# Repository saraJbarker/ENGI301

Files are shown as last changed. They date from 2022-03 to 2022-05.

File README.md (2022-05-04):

<h1>ENGI301</h1>
Repository for ENGI301 course work
<h3>Project 1</h3>
The project_1 folder contains the code for the PocketBeagle Medication Dispenser, found on my Hackster: https://www.hackster.io/sarajbarker/pocketbeagle-medication-dispenser-ca1f8f </br> </br>
All of the hardware can be found on the Hackster page. For the code, the only file needed is <a href=https://github.com/saraJbarker/ENGI301/blob/main/project_1/main_code3.py"">main_code3.py</a>. 
To set up and run this code: </br>
<ol>
  <li> Wire everything up according to the directions on Hackster (also see <a href="https://github.com/saraJbarker/ENGI301/blob/main/project_1/sketch_bb.png"> sketch_bb.png</a> for a Fritzing diagram) </li>
  <li> Connect the PocketBeagle to the internet </li>
  <li> Set up the PocketBeagle to run Python: 
    <ul>
      <li><code>sudo apt-get update </code></li>
      <li><code>sudo apt-get install build-essential python-dev python-setuptools python-smbus -y </code></li>
      <li><code>sudo apt-get install python-pip python3-pip -y</code></li>
    </ul>
  <li>Install Adafruit BBIO:
    <ul><code>sudo pip3 install --upgrade Adafruit_BBIO</code></ul>
    </li>
  <li>Drag and drop <a href=https://github.com/saraJbarker/ENGI301/blob/main/project_1/main_code3.py>main_code3.py</a> into your PocketBeagle directory.</li>
  <li>Press "Run".</li>
  </ol>
  </br>
  Included in the Project 1 folder are the STL and Solidworks files for the pillbox - the STL can go into a 3D printing software like 3DprinterOS, or you can modify the Solidworks file and make a new STL file. <a href="https://github.com/saraJbarker/ENGI301/blob/main/project_1/boxv3all.ai">boxv3all.ai</a> is the Illustrator file for the sides of the wooden box. This can be used with a laser cutter to cut the wood out. <a href="https://github.com/saraJbarker/ENGI301/blob/main/project_1/sketch_bb.png">sketch_bb.png</a> is a picture of the Fritzing file. <code>code_skeleton</code>, <code>main_code.py</code>, and <code>main_code2.py</code> are just in progress versions of the currently updated code, <code>main_code3.py</code> - there isn't a need to download these.
  <h3>Project 2</h3>
  The project_2 folder contains files for a PCB that would control the medication dispenser described in Project 1. The library, schematic, and board files in EAGLE are included in the EAGLE subfolder, and the Gerber files are in the MFG subfolder. If you would like to make this PCB, you will need to send the Gerber files to a manufacturer. There is also a PDF version of the schematic and a Bill of Materials inside the project_2 folder. </br>
  <i>Note:</i> the PCB has not been physically made, so there may be errors in the provided files.

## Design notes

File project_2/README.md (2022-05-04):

The EAGLE folder contains the EAGLE files - library, schematic, and board - to create a PCB that can control the medication dispenser in project_01. The MFG folder contains the Gerber files for the PCB. A bill of materials (Barker_project_02_BOM) and a PDF version of the schematic (Barker_project_02.pdf) is also included.

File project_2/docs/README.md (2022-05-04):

This is the folder that contains pictures of the top and bottom layer as seen in gerbv, a Gerber file viewer.

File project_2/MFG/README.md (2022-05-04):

This is the folder for manufacturing files, including Gerber files and pictures of the top and bottom layers (found in the docs folder).

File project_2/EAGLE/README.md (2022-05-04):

This is the folder for all EAGLE files for the PCB.

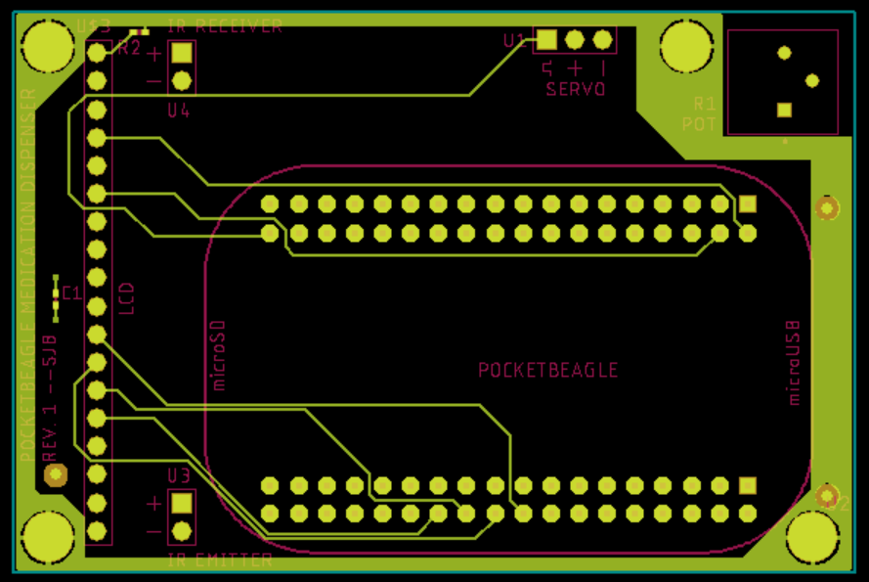
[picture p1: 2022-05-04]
project_2/docs/gerber_file_top.png

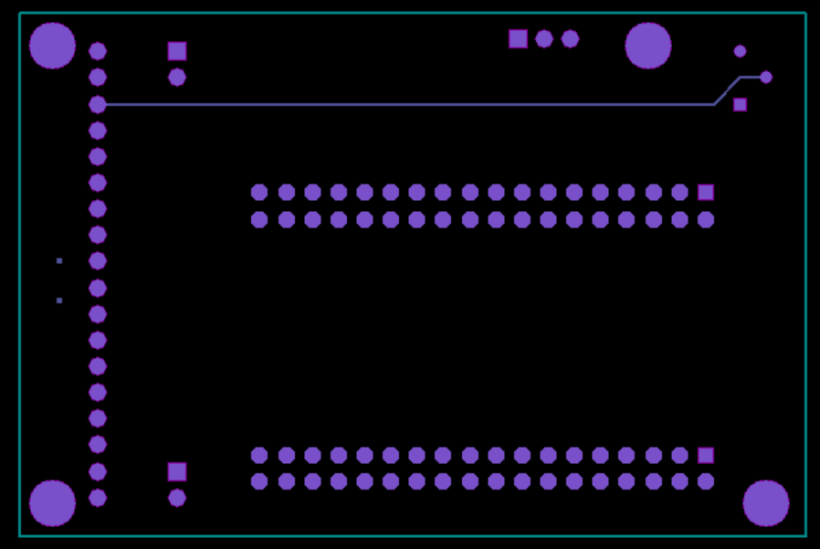
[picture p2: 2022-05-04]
project_2/docs/gerber_file_bottom.png

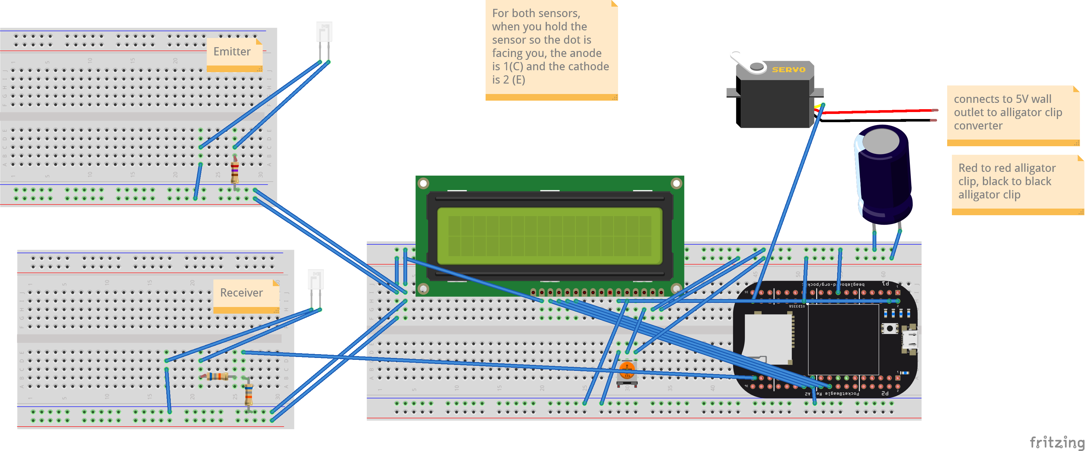
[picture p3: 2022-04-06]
project_1/sketch_bb.png

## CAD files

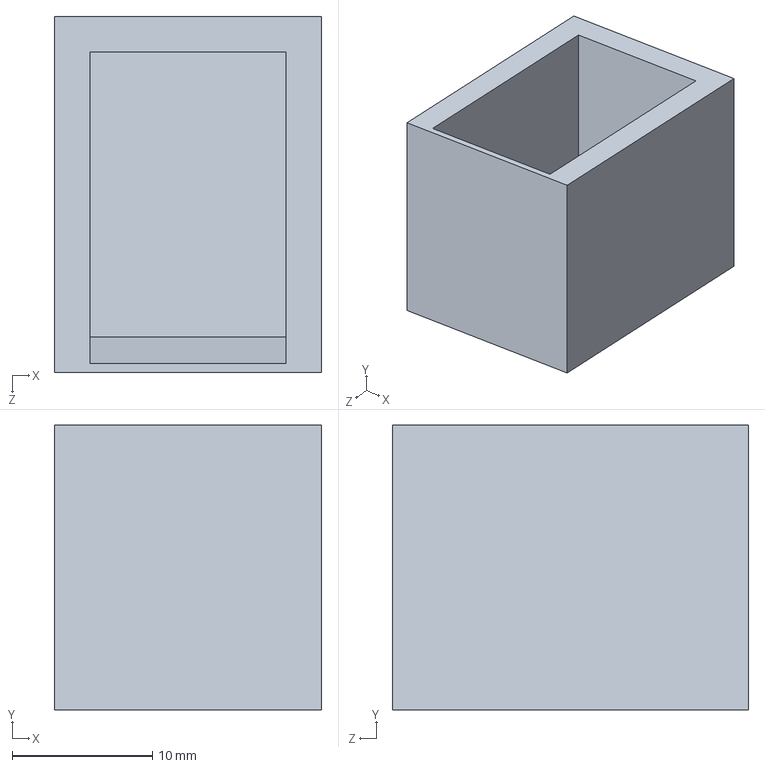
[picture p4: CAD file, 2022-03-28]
project_1/box.SLDPRT
19.1 x 20.3 x 25.4 mm

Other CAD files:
project_1/box.STL

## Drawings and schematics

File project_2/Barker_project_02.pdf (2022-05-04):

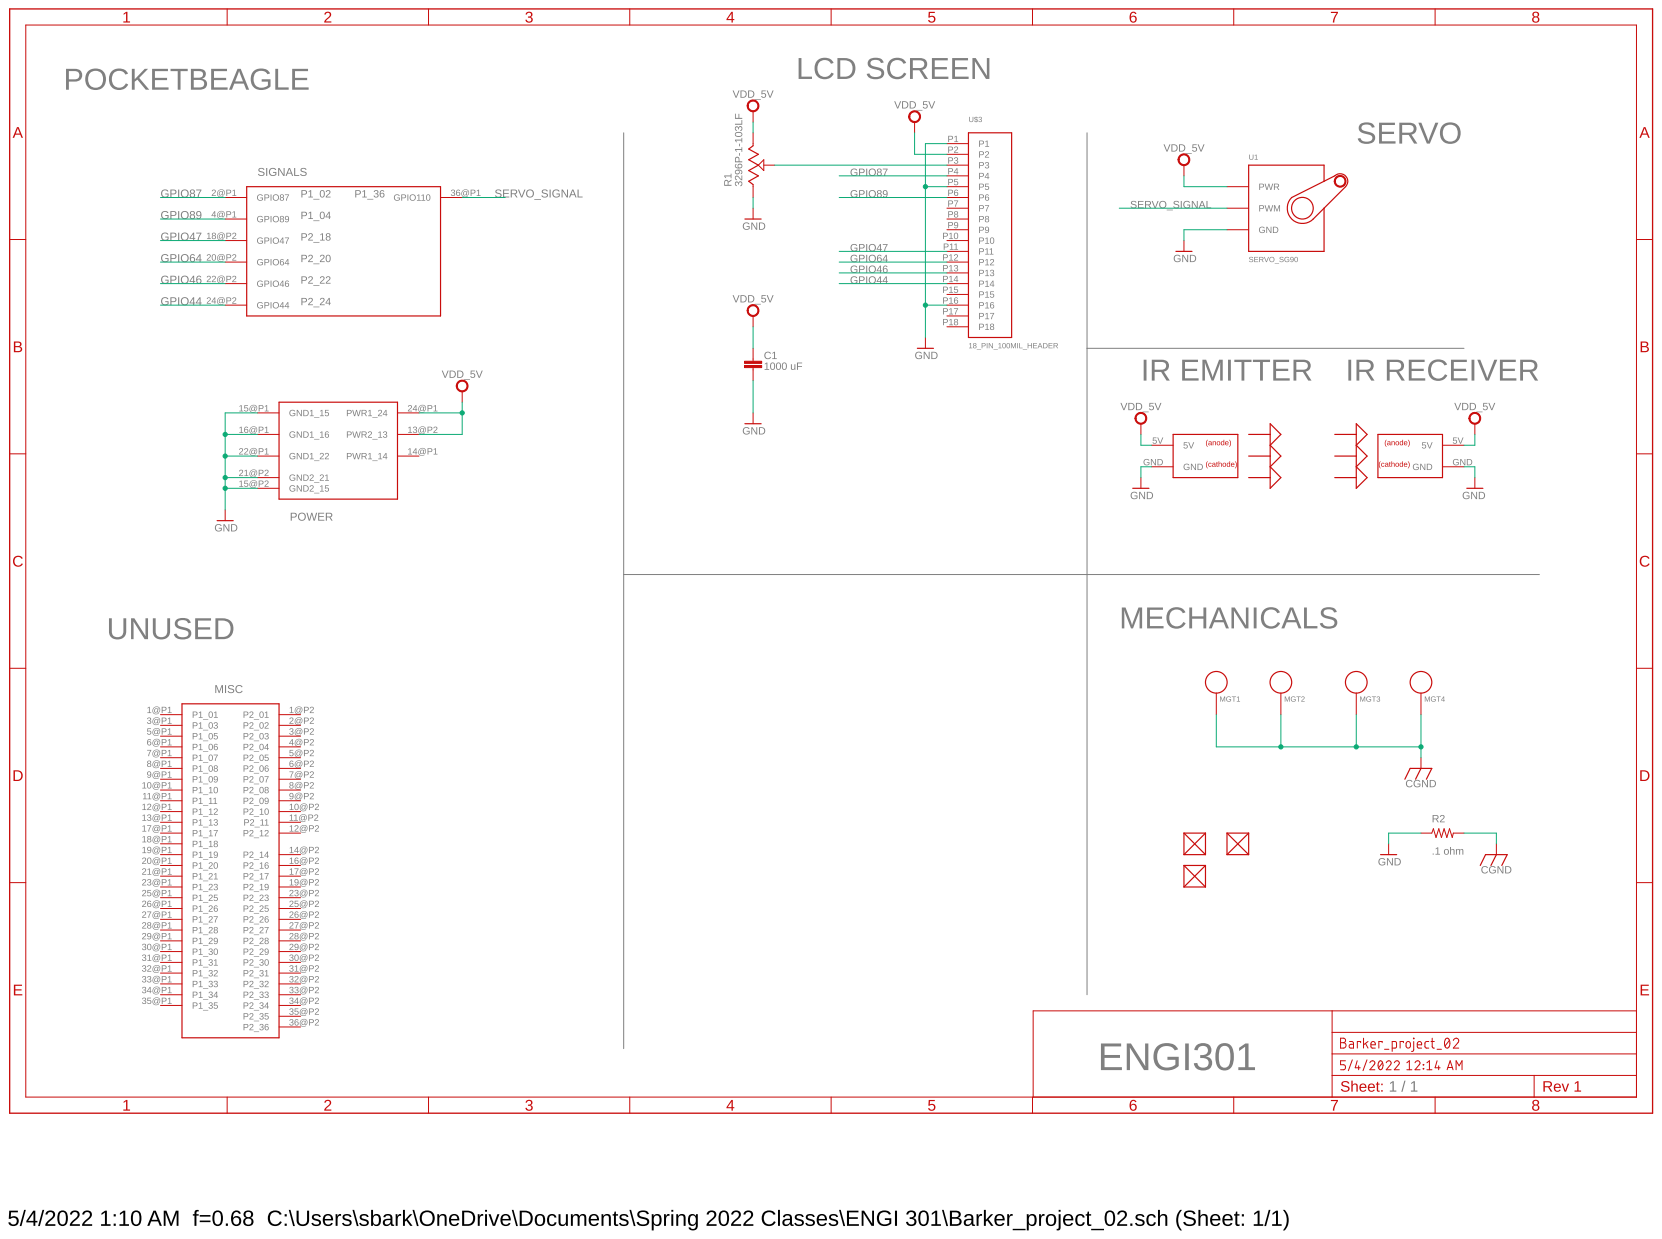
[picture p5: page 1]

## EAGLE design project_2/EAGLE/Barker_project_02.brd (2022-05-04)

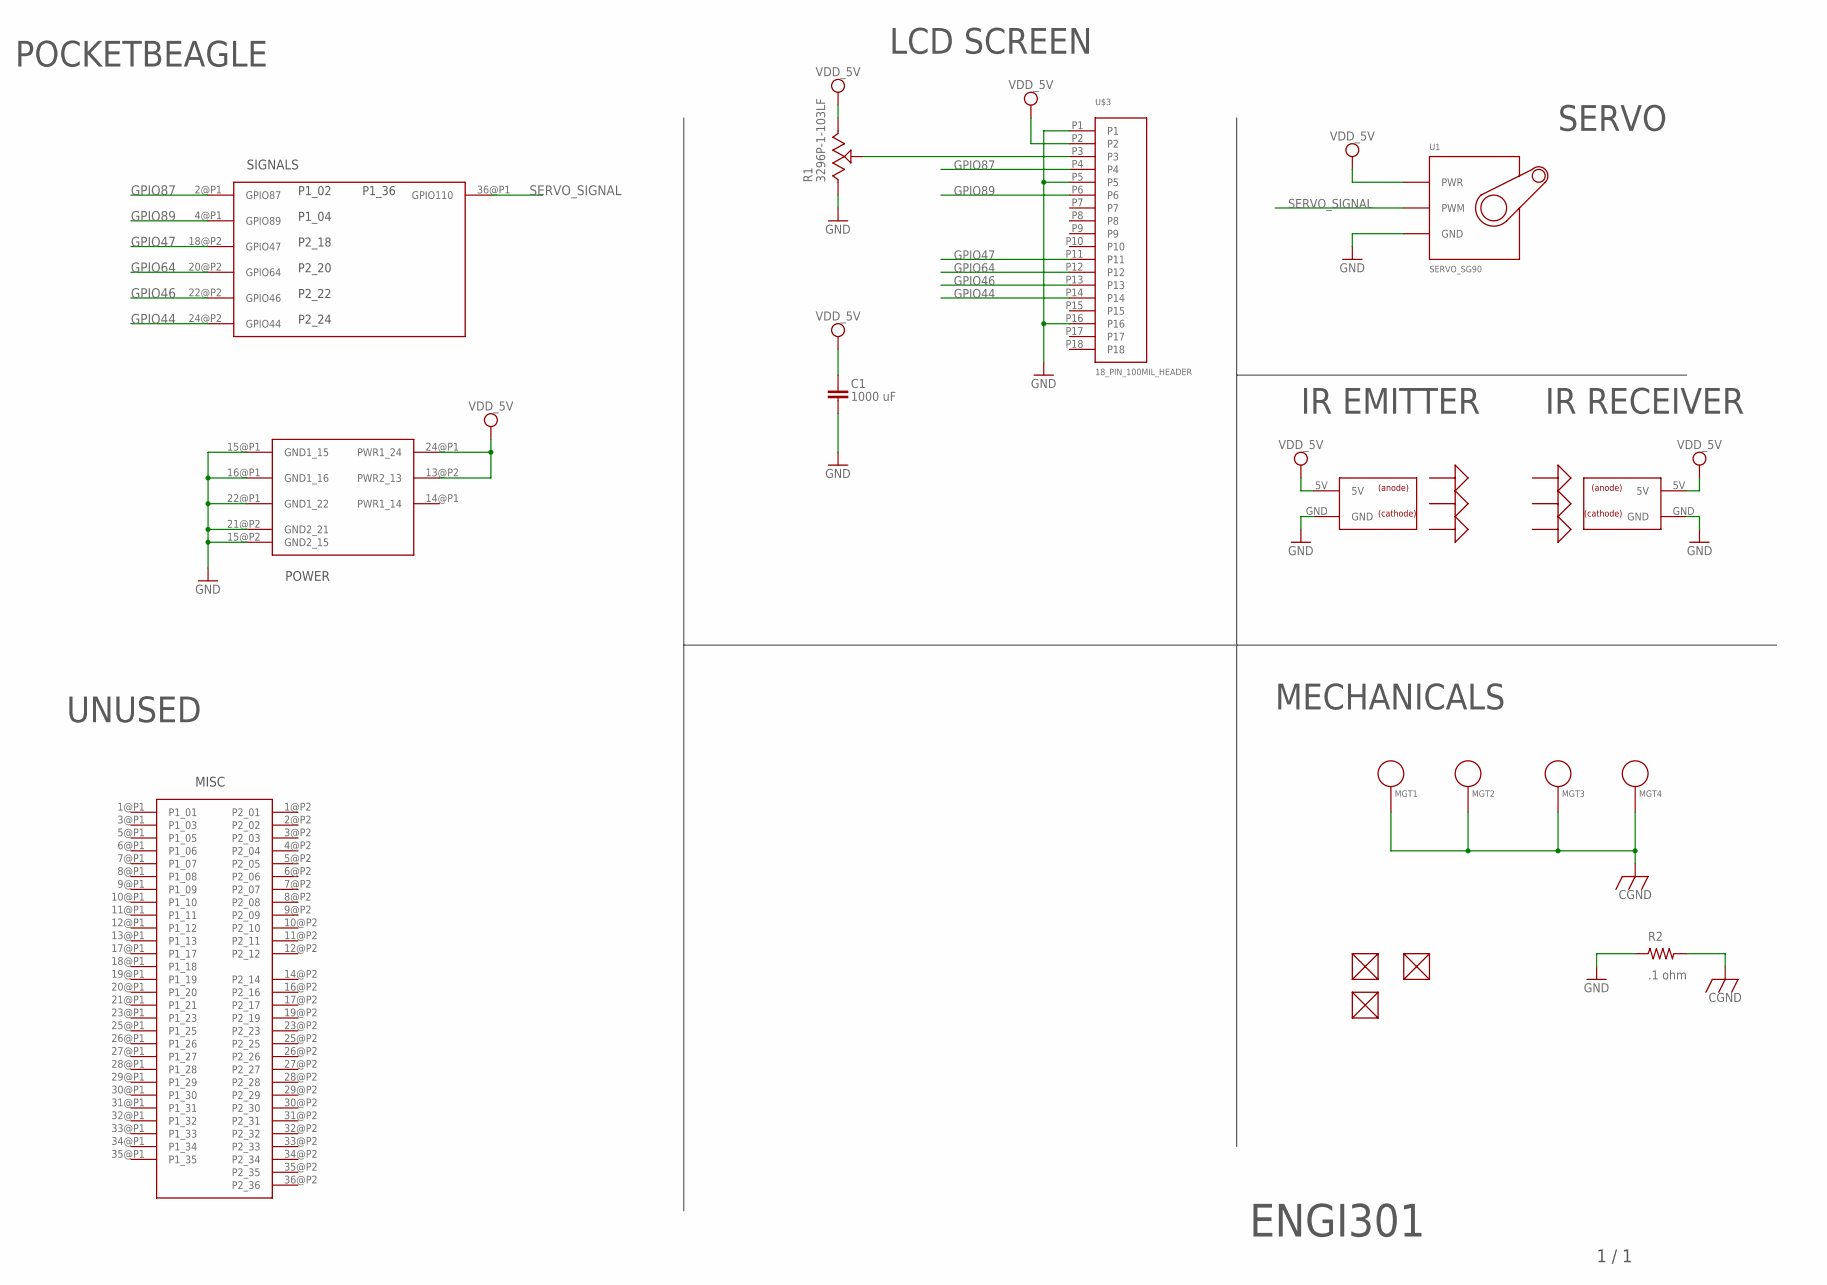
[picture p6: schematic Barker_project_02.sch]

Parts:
C1: 1000 uF; C0402
FUD1, FUD2, FUD3: FIDUCIAL; FIDUCIAL_40MIL
MGT1, MGT2, MGT3, MGT4: MOUNTING_HOLE
R1: 3296P-1-103LF; TRIM_3296P-1-103LF
R2: .1 ohm; R0402
U1: SERVO_SG90; SERVO-X1
U2: POCKETBEAGLE
U3: IR_EMITTER; 2_PIN_100MIL_HEADER
U4: IR_DETECTOR; 2_PIN_100MIL_HEADER
U$3: 18_PIN_100MIL_HEADER

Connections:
CGND: MGT1.P$1, MGT2.P$1, MGT3.P$1, MGT4.P$1, R2.2
GND: C1.2, R1.1 (CCW), R2.1, U1.GND, U2.15@P1 (GND1_15), U2.15@P2 (GND2_15), U2.16@P1 (GND1_16), U2.21@P2 (GND2_21), U2.22@P1 (GND1_22), U3.GND, U4.GND, U$3.P1, U$3.P5, U$3.P16
GPIO44: U2.24@P2 (GPIO44), U$3.P14
GPIO46: U2.22@P2 (GPIO46), U$3.P13
GPIO47: U2.18@P2 (GPIO47), U$3.P11
GPIO64: U2.20@P2 (GPIO64), U$3.P12
GPIO87: U2.2@P1 (GPIO87), U$3.P4
GPIO89: U2.4@P1 (GPIO89), U$3.P6
unnamed: R1.2 (WIPER), U$3.P3
SERVO_SIGNAL: U1.SIG (PWM), U2.36@P1 (GPIO110)
VDD_5V: C1.1, R1.3 (CW), U1.PWR, U2.13@P2 (PWR2_13), U2.24@P1 (PWR1_24), U3.5V, U4.5V, U$3.P2

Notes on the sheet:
IR RECEIVER
IR EMITTER
SERVO
LCD SCREEN
POCKETBEAGLE
MECHANICALS
POWER
SIGNALS
MISC
ENGI301
1 / 1
UNUSED

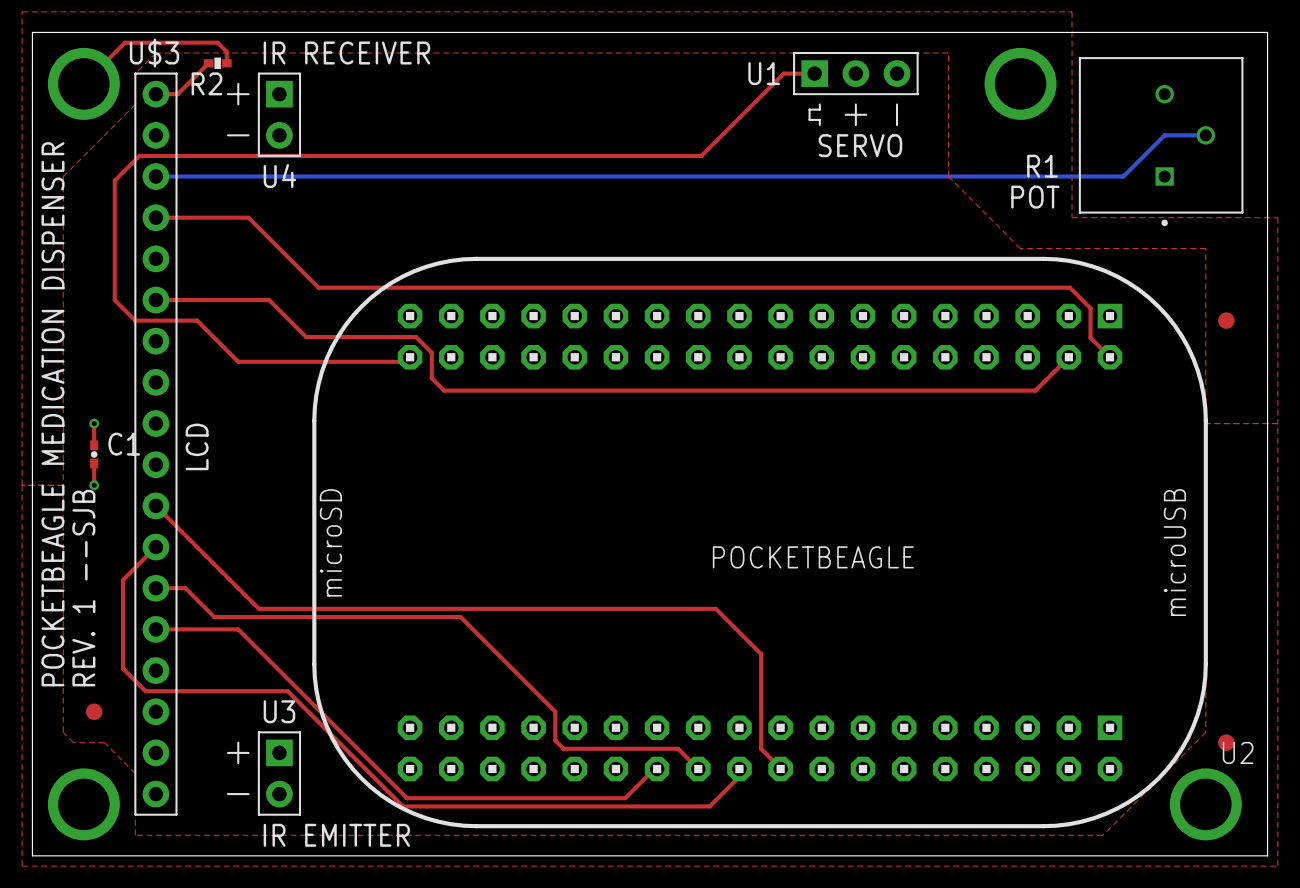
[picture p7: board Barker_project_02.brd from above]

Board: 4 copper layers, 76.2 x 50.8 mm, 15 parts (0 on the bottom side), 11 nets.

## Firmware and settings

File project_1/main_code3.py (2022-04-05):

"""
--------------------------------------------------------------------------
Medication Dispenser
--------------------------------------------------------------------------
License:   
Copyright 2022 Sara Barker

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
1. Redistributions of source code must retain the above copyright notice, this 
list of conditions and the following disclaimer.

2. Redistributions in binary form must reproduce the above copyright notice, 
this list of conditions and the following disclaimer in the documentation 
and/or other materials provided with the distribution.

3. Neither the name of the copyright holder nor the names of its contributors 
may be used to endorse or promote products derived from this software without 
specific prior written permission.

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
The display code borrows from code written by Angelica Torres.
(https://github.com/alt7rice/ENGI301/blob/main/project_01/rgb_lcd/rgb_lcd_test.py)
Their licensing information is: 
  - SPDX-FileCopyrightText: Copyright 2021 Angelica Torres
  - SPDX-License-Identifier: MIT
  
The IR code borrows from code written by Adafruit.
(https://learn.adafruit.com/ir-breakbeam-sensors/circuitpython)


--------------------------------------------------------------------------

This program operates a conveyor belt, driven by a servo motor, that drops medication into
a user's hand when they place their hand under the dispensing area and block an IR beam.

Requirements:
  - If the dispenser has not been used today, and a hand blocks the IR beam, move the conveyor
    belt forward to dispense the pills in the next full pillbox.
  - If the IR beam is blocked and pills have already been taken for the day (*in this code, 10s.), do nothing with the motor, 
  -     and display a message stating that it is too soon to take more pills.
  - Display message every 7 days (*in this code, 1 minute) to remind users to refill pills.

Uses:
  - time
  - Adafruit BBIO
  - board
  - digitalio
  - Adafruit character lcd

"""
import time
import Adafruit_BBIO.PWM as PWM
import Adafruit_BBIO.ADC as ADC


#needed for display
import board
import digitalio
import adafruit_character_lcd.character_lcd as charlcd


# ------------------------------------------------------------------------
# Constants
# ------------------------------------------------------------------------

#constants for servo
SG90_FREQ   = 333                  # 20ms period (50Hz)
SG90_POL    = 0                   # Rising Edge polarity
SG90_OFF    = 50                   # 0ms pulse -- Servo is inactive
SG90_RIGHT  = 15                   # 1ms pulse (15% duty cycle)  -- All the way right
SG90_LEFT   = 80                 # 2ms pulse (80% duty cycle) -- All the way Left


# ------------------------------------------------------------------------
# Functions / Classes
# ------------------------------------------------------------------------

class Servo():
    servo      = None
    
    def __init__(self, servo="P1_36"):
        """ Initialize variables and set up display """
        self.servo      = servo
        
        self._setup()
    
    # End def
    
    
    def _setup(self):
        """Setup the hardware components."""
        # Initialize Servo; Servo should be "off"
        PWM.start(self.servo, SG90_OFF, SG90_FREQ, SG90_POL)

    # End def


    def moveBack(self):
        #move servo counterclockwise to move conveyor belt back
        PWM.set_duty_cycle(self.servo, SG90_LEFT)
        time.sleep(0.5)

    # End def


    def moveFwd(self):
        #move servo clockwise to advance conveyor belt to next day
        PWM.set_duty_cycle(self.servo, SG90_RIGHT)
        time.sleep(0.5)
        

    # End def
    
    def zero(self):
        #make servo stop
        PWM.set_duty_cycle(self.servo, SG90_OFF)
    # End def

    def cleanup(self):
        """Cleanup the hardware components."""
        
        # Stop servo
        PWM.set_duty_cycle(self.servo, SG90_OFF)
        
    # End def
    
    def dispense(self, lastDispenseTime):
        #if current time is more than 10 seconds past the last time medication was dispensed, move the servo forward
        if ((time.time() - lastDispenseTime) > 10):
            self.moveFwd()
            self.zero()
            return True
        else:
            display.write("You already took\ntoday's dose.")
            time.sleep(5)
            display.blank()
            return False
            
    def refill(self):
        #moves the motor backward until it reaches the starting position again
        self.moveBack()
        time.sleep(4)
        self.zero()
        

# End class

class Display():
    lcd     = None
    rows    = None
    columns = None
    
    
    def __init__(self, rs=board.P1_2, en=board.P1_4, d7=board.P2_24, d6=board.P2_22, d5=board.P2_20, d4=board.P2_18):
        self.rows    = 2
        self.columns = 16
        
        lcd_rs = digitalio.DigitalInOut(rs)
        lcd_en = digitalio.DigitalInOut(en)
        lcd_d7 = digitalio.DigitalInOut(d7)
        lcd_d6 = digitalio.DigitalInOut(d6)
        lcd_d5 = digitalio.DigitalInOut(d5)
        lcd_d4 = digitalio.DigitalInOut(d4)
        
        self.lcd = charlcd.Character_LCD_Mono(
            lcd_rs, lcd_en, lcd_d4, lcd_d5, lcd_d6, lcd_d7, self.columns, self.rows
        )
        
        self._setup()
    #end def
    
    def _setup(self):
        self.blank()
    #end def
    
    def blank(self):
        #clear the screen
        self.lcd.message = "                \n                "
        time.sleep(0.5)
    # End def
        
    def write(self, message):
        self.lcd.message = message
        time.sleep(0.5)
    #end def
    
    
#End class

class IR():
    analog_in = None
    
    def __init__(self, analog_in = "AIN5"):
        self.analog_in = analog_in
        self._setup()
        
        
    def _setup(self):
        ADC.setup()
        
    def getValue(self):
        value = ADC.read_raw(self.analog_in)
        return value
        
    
    
#end class

    


# ------------------------------------------------------------------------
# Main script
# ------------------------------------------------------------------------

if __name__ == '__main__':
    #use the time at bootup as the start time (used as a reference time)
    startTime = time.time()
    
    #initialize time at boot as last dispense time
    lastDispenseTime = time.time() 
    dayCounter = 0
    
    #instantiate instances of classes
    IRvalue = IR()
    servo = Servo()
    display = Display()
    
    display.blank()
    
    while(1):
         #<400 means beam is blocked
        if (IRvalue.getValue() < 300):
            #check if last dispense time is more than 10 seconds past the current time
                #if yes, dispense pills
            if (servo.dispense(lastDispenseTime)):
                servo.moveFwd()
                servo.zero()
                #store the current time as the last dispense time
                lastDispenseTime = time.time()
                dayCounter = dayCounter+1
                print(dayCounter)
            
            #warn user if it's been too long between doses
            #set to 60s for purposes of testing
        if ((time.time()-lastDispenseTime) > 60):
            startTime = time.time()
            display.write("You need to take\nyour pills soon")
        #if all the pills are dispensed (i.e. boxes 0-6 are empty), reset the belt
        if (dayCounter == 6):
                display.blank()
                display.write("Time to refill!")
                time.sleep(5)
                display.blank()
                dayCounter = 0
                servo.refill()
            #check for the IR value every 0.1s
        time.sleep(0.1)
            

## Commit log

2022-03-28 Add STL and Solidworks files for pill boxes
    [box.SLDPRT, box.STL]
2022-03-30 Added Solidworks and STL files for pill boxes
    [box.SLDPRT, box.STL]
2022-05-04 Add Bill of Materials
2022-05-04 Added Board and Schematic files
    [Barker_project_02.brd, Barker_project_02.sch]
2022-05-04 Added Schematic and Board files
    [Barker_project_02.brd, Barker_project_02.sch]
2022-05-04 Added Gerber files
    [copper_bottom_l4.gbr, copper_inner_l2.gbr, copper_inner_l3.gbr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]
2022-05-04 Added pictures of top and bottom of board
2022-05-04 Added schematic PDF
